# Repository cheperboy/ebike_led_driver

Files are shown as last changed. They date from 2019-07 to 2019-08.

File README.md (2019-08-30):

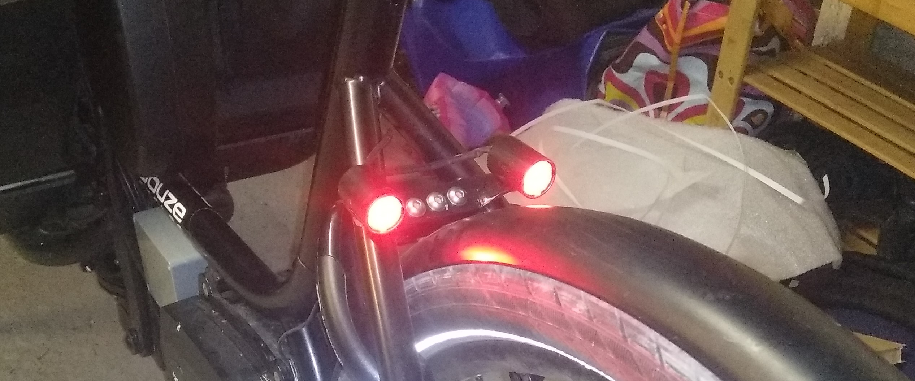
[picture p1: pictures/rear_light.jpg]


# Motivation
Find it so weird to recharge almost every day a dedicated battery for the rear light of my cargo e-bike while a there is a huge battery onboard available on this bike to power the motor!

Power leds (3W) became so cheap and come with optics, it is perfect for any project needing efficient light system.
 
# Objective
The goal of this project is to realize a e-bike front/rear led lamp with following constraints:
1. Powered from dedicated 6v/2A power from the motor’s controller (Brose motor). No power bank or other battery than the e-bike battery!
2. Visibility / Efficiency as much as possible
3. As far as possible, a gentle design for led housing, well integrated to the bike frame (Douze Cycle cargo bike)
 
# Main design choices
* Use of Cree XP-E2 Led (front light: neutral white. Rear light: red)
* Led driver based on MOSFET and BJT transistor : cheap, versatile  
* Led housing made of 3/4" copper pipe (fits perfectly for XP-E2 leds)
 
# Circuit design
The available power from Brose motor is 14.6 W whose 3.6 W already used by a manufactured front lamp installed on the bike -> 11 W available for this project

## Schematic
See [constant current instructable led driver circuit](https://www.instructables.com/id/Power-LED-s---simplest-light-with-constant-current/) : Cheap and efficient, could work with input voltage up to 60 V. Low drop out voltage between input and output so it can drive two led in series from 6 volt input.

The value of R_sense limit the current through the led to 1A.

Dimming the led is achieved with pwm from Attiny85.

Rear light
The rear light has two modes:

Constant low power
Blink: alternate low power / high power light (best approach for visibility purpose)
Constant low power: pwm ratio is 10/255 -> about 0,25W

Blink: pwm ratio is 10/255 during 500 ms and 60/255 during 50 ms. -> about 0,35 W 

Then about 10W still available for the front light (more than enough!)

Front light
The front light has two modes: OFF / ON (pwm dimmed to every available amps)

Below the general principle of the schematic.
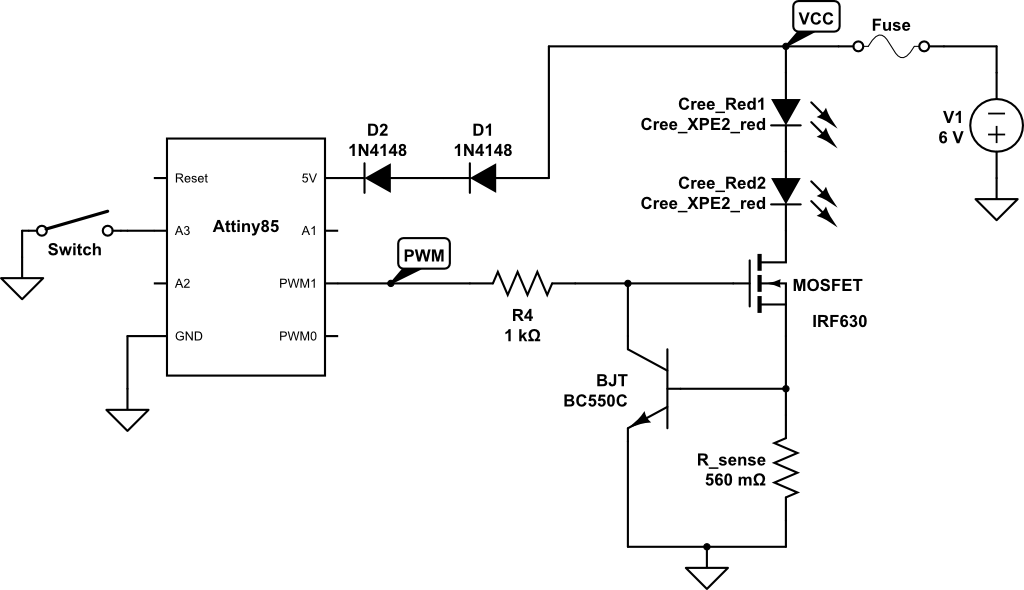
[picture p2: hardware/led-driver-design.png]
CircuitLab


## PCB / stripboard design
Components are soldered on a stripboard. it was intended to be a prototype but became the final circuit because works well and perfectly fits in the box.
Below the design of PCB including two drivers (front and rear lights).
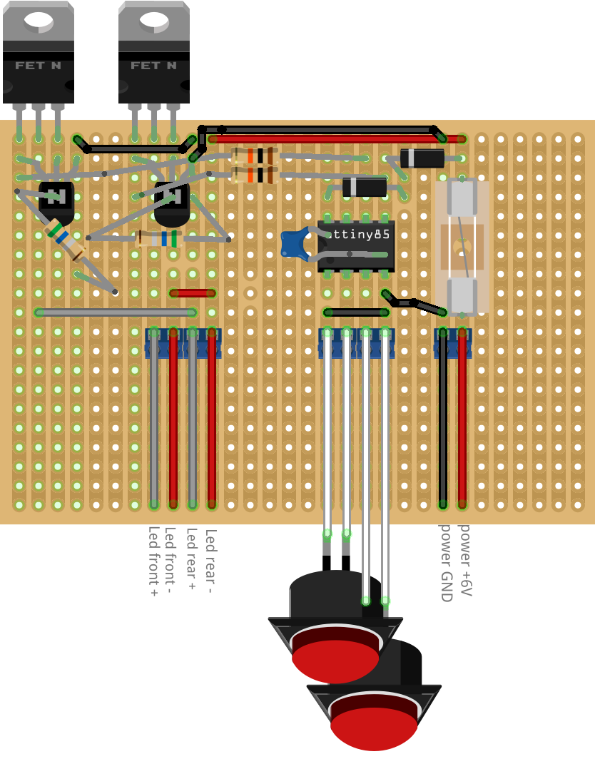
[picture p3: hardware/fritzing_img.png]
fritzing design


## PCB soldered
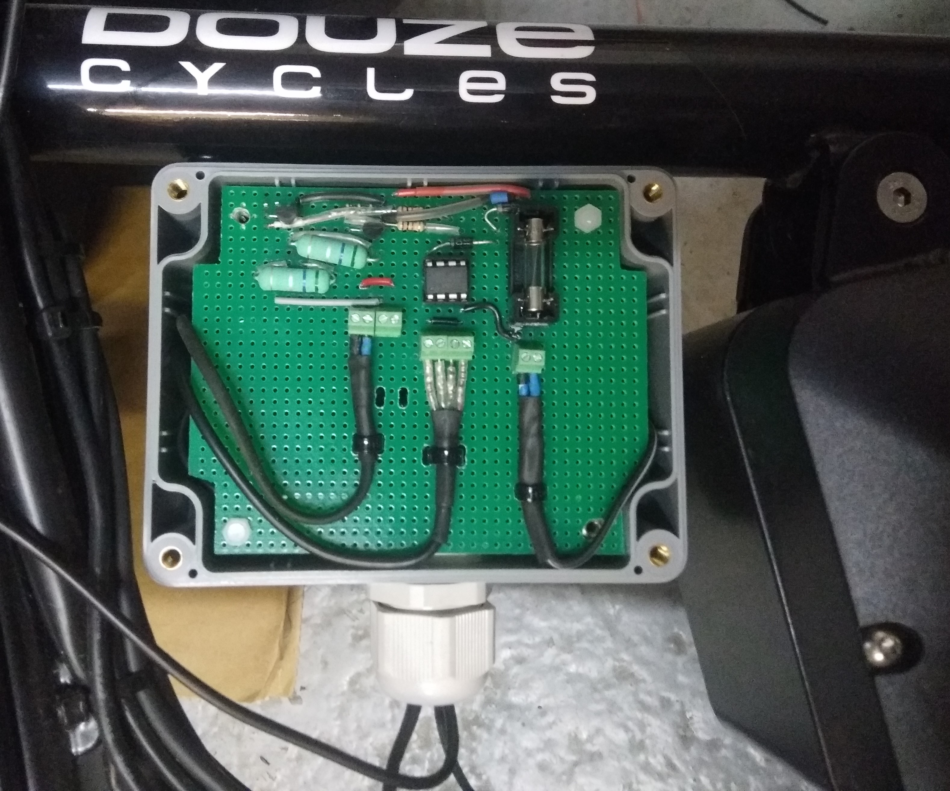
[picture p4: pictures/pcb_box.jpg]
PCB soldered


# Led Housing
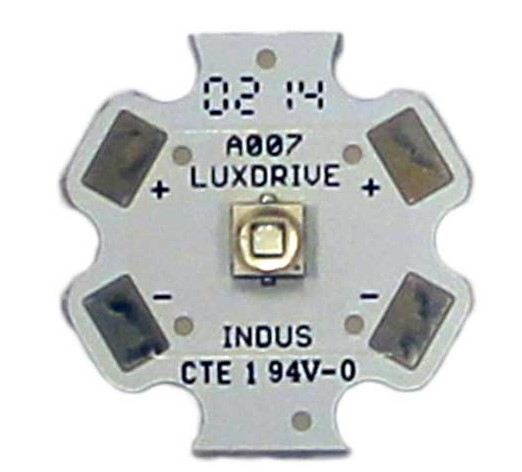
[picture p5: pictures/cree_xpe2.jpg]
cree_xpe2
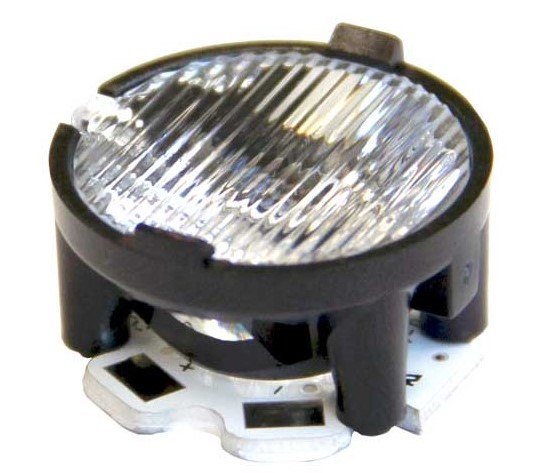
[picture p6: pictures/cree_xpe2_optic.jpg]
cree_xpe2_optic
|  |   |
|---|---|

Cree Led XP-E2 mounted on a 20 mm diameter pcb.
3/4" copper pipe has exactly enough room to hold it.
Led pcb is glued inside the tube.
The tube is mounted on a twisted aluminum plate.

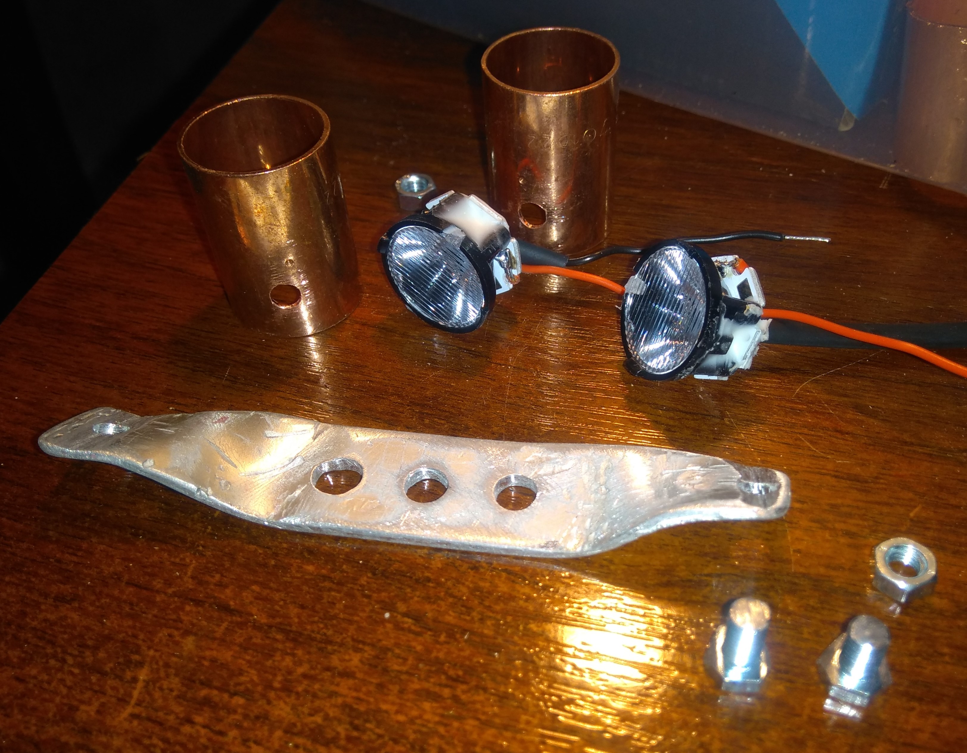
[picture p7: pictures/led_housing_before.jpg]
led_housing_before
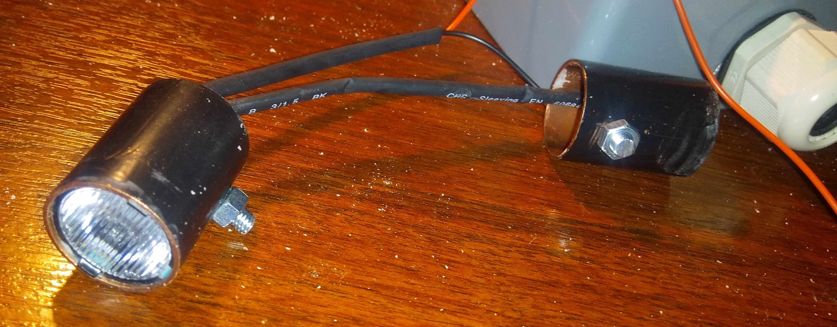
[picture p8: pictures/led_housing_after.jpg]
led_housing_after
|  |   |
|---|---|

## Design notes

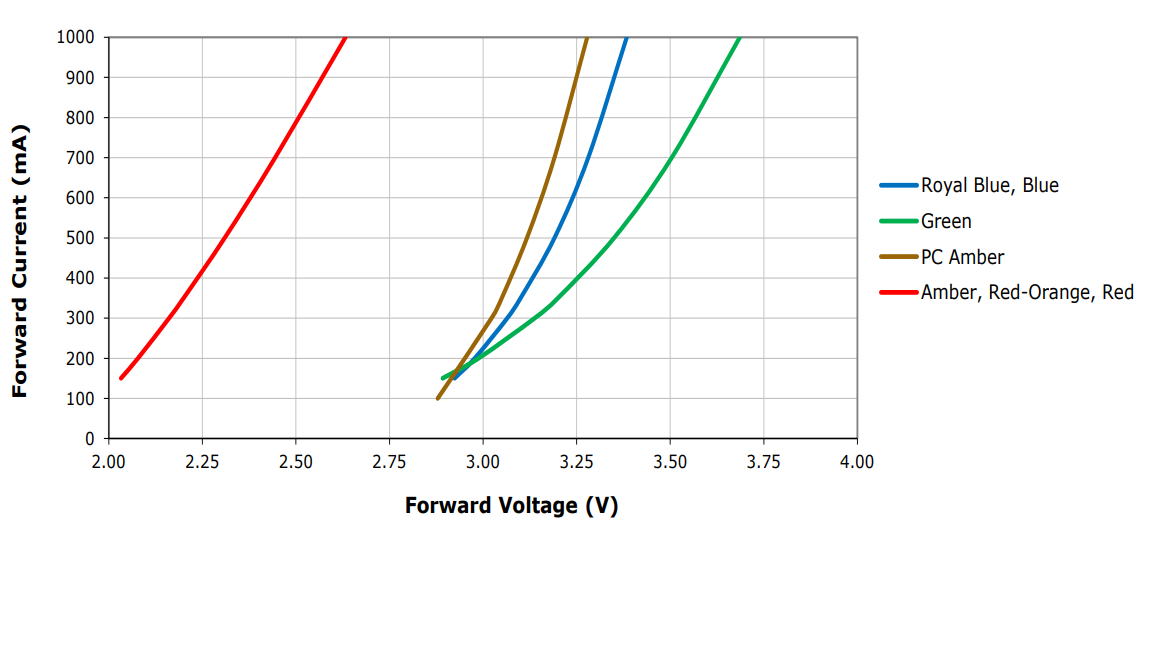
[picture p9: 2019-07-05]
hardware/CREE current vs voltage.png

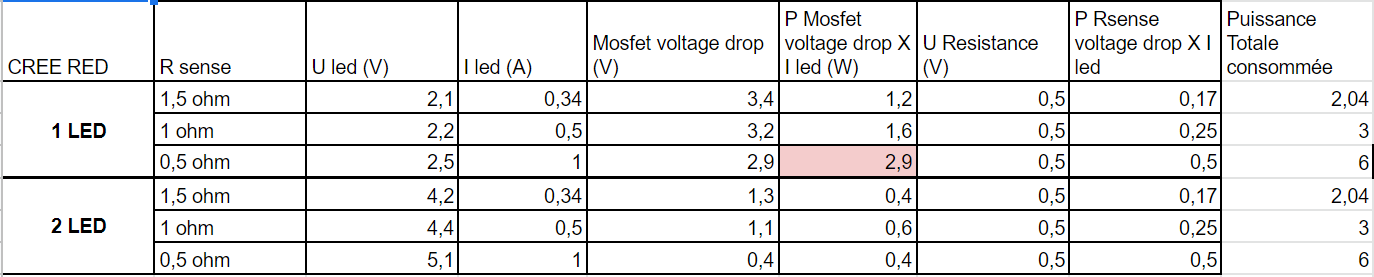
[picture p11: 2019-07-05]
hardware/calculs.png

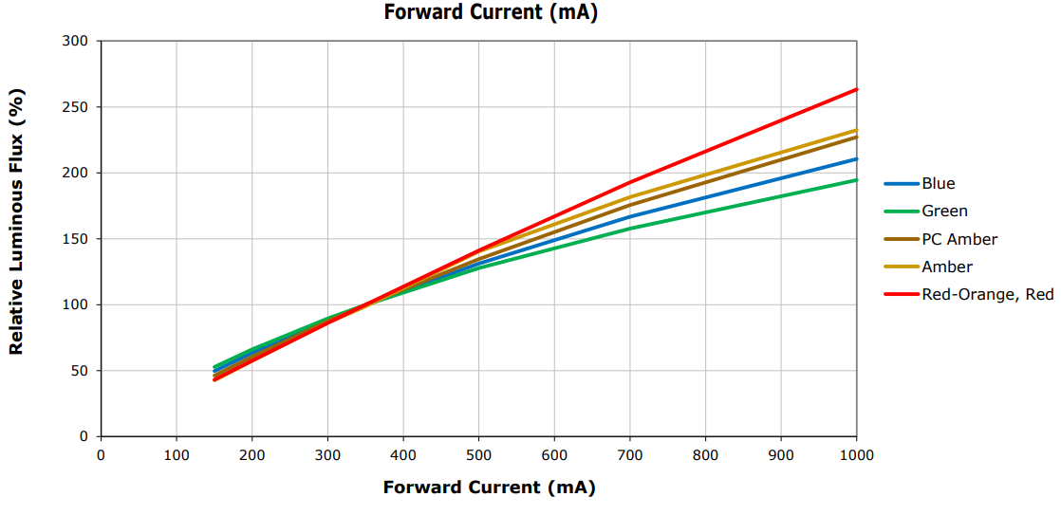
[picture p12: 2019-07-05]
hardware/CREE flux vs current.png

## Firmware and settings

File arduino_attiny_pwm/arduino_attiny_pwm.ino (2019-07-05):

/*
Use of timer to blink led
Library fit for Attiny85
https://github.com/PaulStoffregen/TimerOne/blob/master/examples/ATTiny85/ATTiny85.ino	
*/

#include <TimerOne.h>

// PIN assignement
#define out_pwm_rear 	0 	// PB0 Pin5 OUTPUT PWM Front Led
#define out_pwm_front 	1 	// PB1 Pin6 OUTPUT PWM Rear led
#define in_button_rear 	A2 	// A2 Pin3 INPUT_PULLUP button
#define in_button_front A3 	// A3 Pin2 INPUT_PULLUP button

// Brightness PWM values
#define brightness_rear_low 	10
#define brightness_rear_high 	60

// Delay timer values
#define delay_rear_led_low 	500000 // 500 ms
#define delay_rear_led_high 50000 // 50 ms

// State memorisation
int rear_led_state = LOW;
int requested_state = LOW;

void setup() {
	pinMode(out_pwm_rear, 	 OUTPUT);
	pinMode(out_pwm_front,	 OUTPUT);
	pinMode(in_button_rear,  INPUT_PULLUP);
	pinMode(in_button_front, INPUT_PULLUP);
	Timer1.initialize(delay_rear_led_low); // Enable Timer1
	analogWrite(out_pwm_rear, brightness_rear_low);
}

void manage_led_rear(bool requested_state) {
	if (requested_state == LOW) {
		Timer1.detachInterrupt(); // Disable Timer1
		analogWrite(out_pwm_rear, brightness_rear_low); // produces PWM (range 0 to 255) with low brightness
	}
	else {
		blink_rear_led();
	}
}
void blink_rear_led(){
	/* Manage rear led blinking
	low pwm value during delay_rear_led_low
	high pwm value during delay_rear_led_high
	*/
	if (rear_led_state == HIGH)
	{
		analogWrite(out_pwm_rear, brightness_rear_low);
		rear_led_state = LOW;
		Timer1.initialize(delay_rear_led_low);
		Timer1.attachInterrupt(blink_rear_led);	
	}
	else
	{
		analogWrite(out_pwm_rear, brightness_rear_high);
		rear_led_state = HIGH;
		Timer1.initialize(delay_rear_led_high);
		Timer1.attachInterrupt(blink_rear_led);	
	}
}

void loop()
{	
	if (requested_state != digitalRead(in_button_rear)){
		requested_state = !requested_state;
		manage_led_rear(requested_state);
	}
}
